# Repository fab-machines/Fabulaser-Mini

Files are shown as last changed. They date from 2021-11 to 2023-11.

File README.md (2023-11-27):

<div align="center"><h1 style=align="center">Fabulaser Mini V3</h1></div>
<div align="center"><i>An open source laser cutter within your reach.</i></div>

<br>
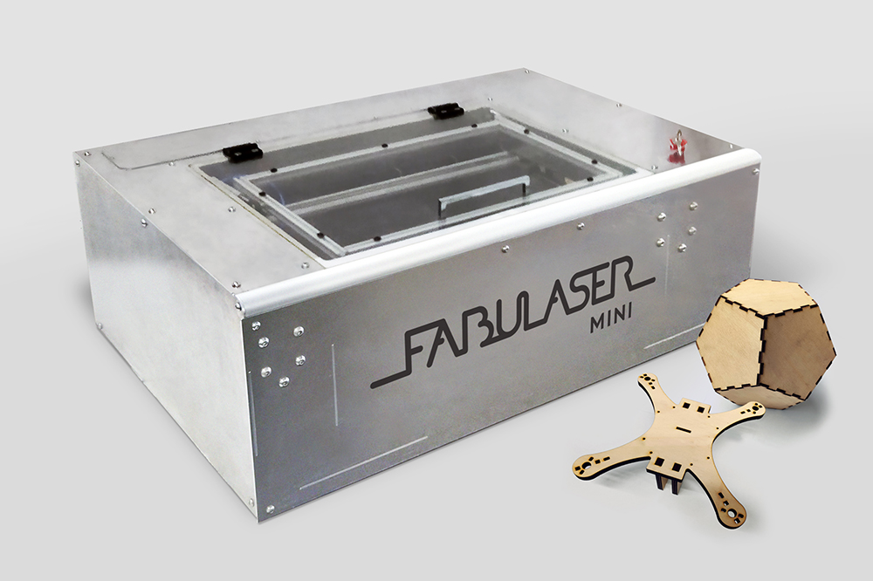
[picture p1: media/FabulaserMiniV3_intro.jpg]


Introduction 
---
Fabulaser Mini is a compact, yet  powerful, open source laser cutter. Developed to fit in Fab Labs and classrooms, Fabulaser Mini aims to lower the boundaries of accessing laser cutting technology, representing an ideal compromise between performance and cost. With an optimized 40W CO2 laser, it is able to cut 8mm acrylic, and with a cutting area of 600x400mm is one the largest of this machine category. The compact machine size of 1161x812x390mm, allows the usage in small rooms with a normal table or a desk.

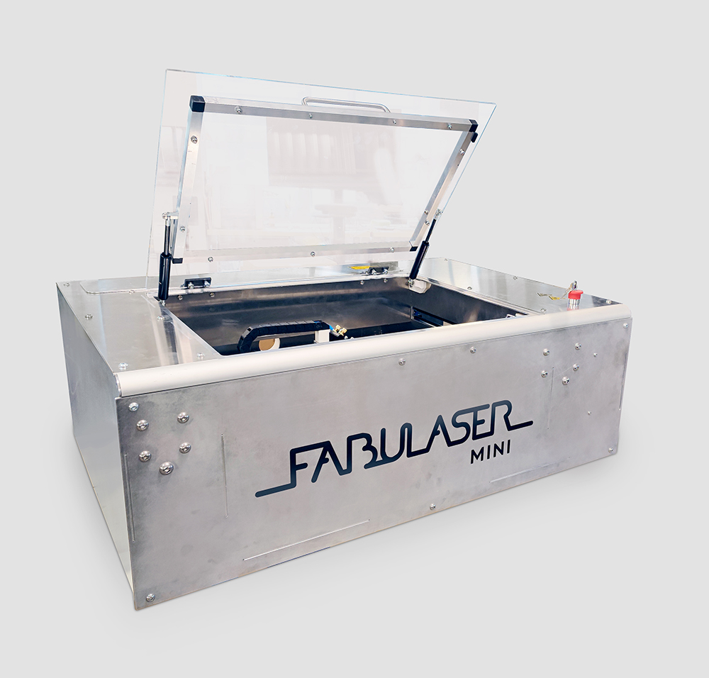
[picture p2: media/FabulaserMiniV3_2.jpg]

<br>

A tool to make, a tool to learn.
--

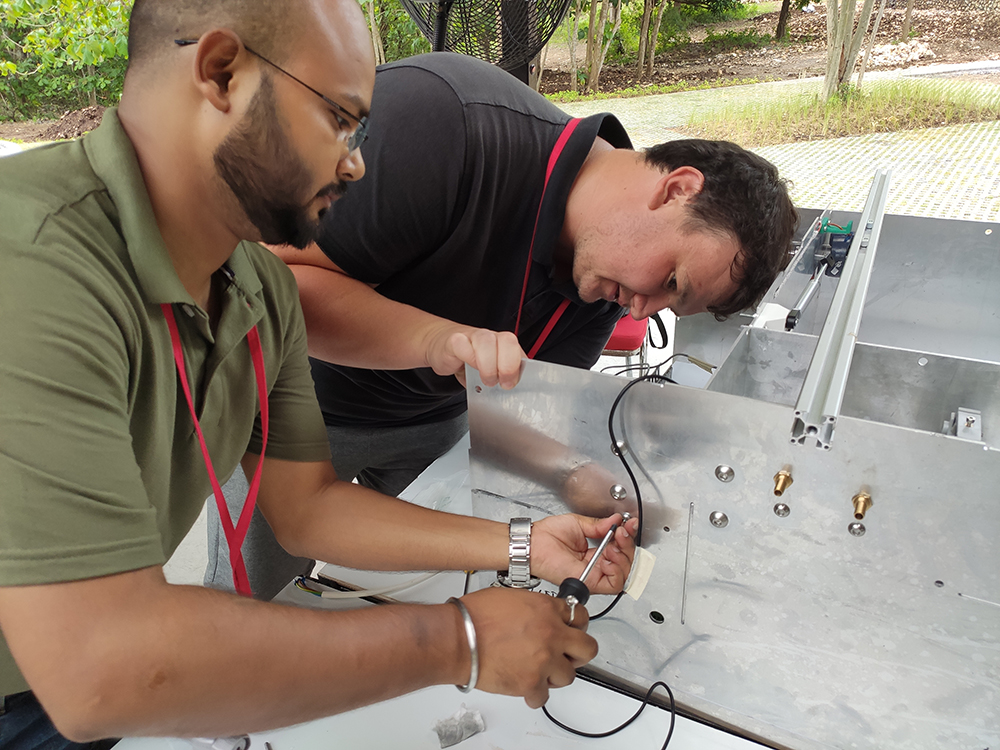
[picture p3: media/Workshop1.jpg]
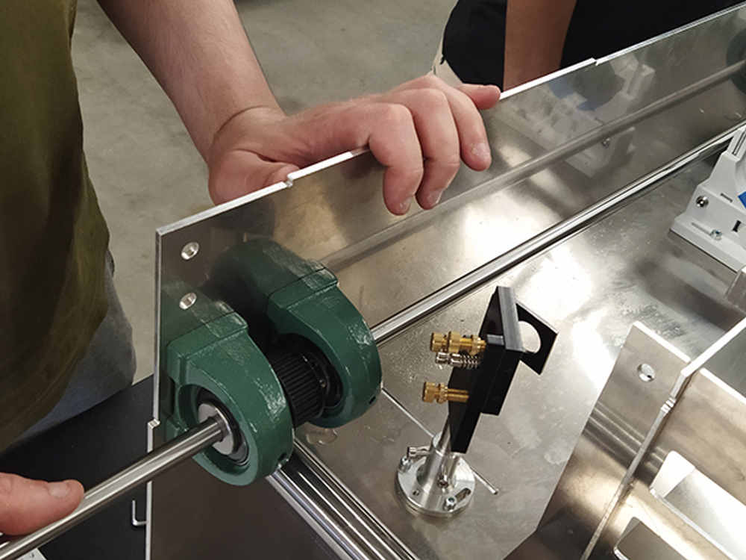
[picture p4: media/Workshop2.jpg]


In comparison to commercial laser cutters, Fabulaser Mini adds on top of the laser cutting functionalities a valuable learning experience. Ideally built together with students during a workshop, Fabulaser Mini will give to the user not only the possibility to laser cut, but also to learn how the machine is made, how it works. And other than learning about electronics, mechanics and lasers, the final user will also have a deep knowledge of the machine, so to be able to efficiently execute maintenance, apply improvements and even design his own machine later on!

The Assembly Manual 
--
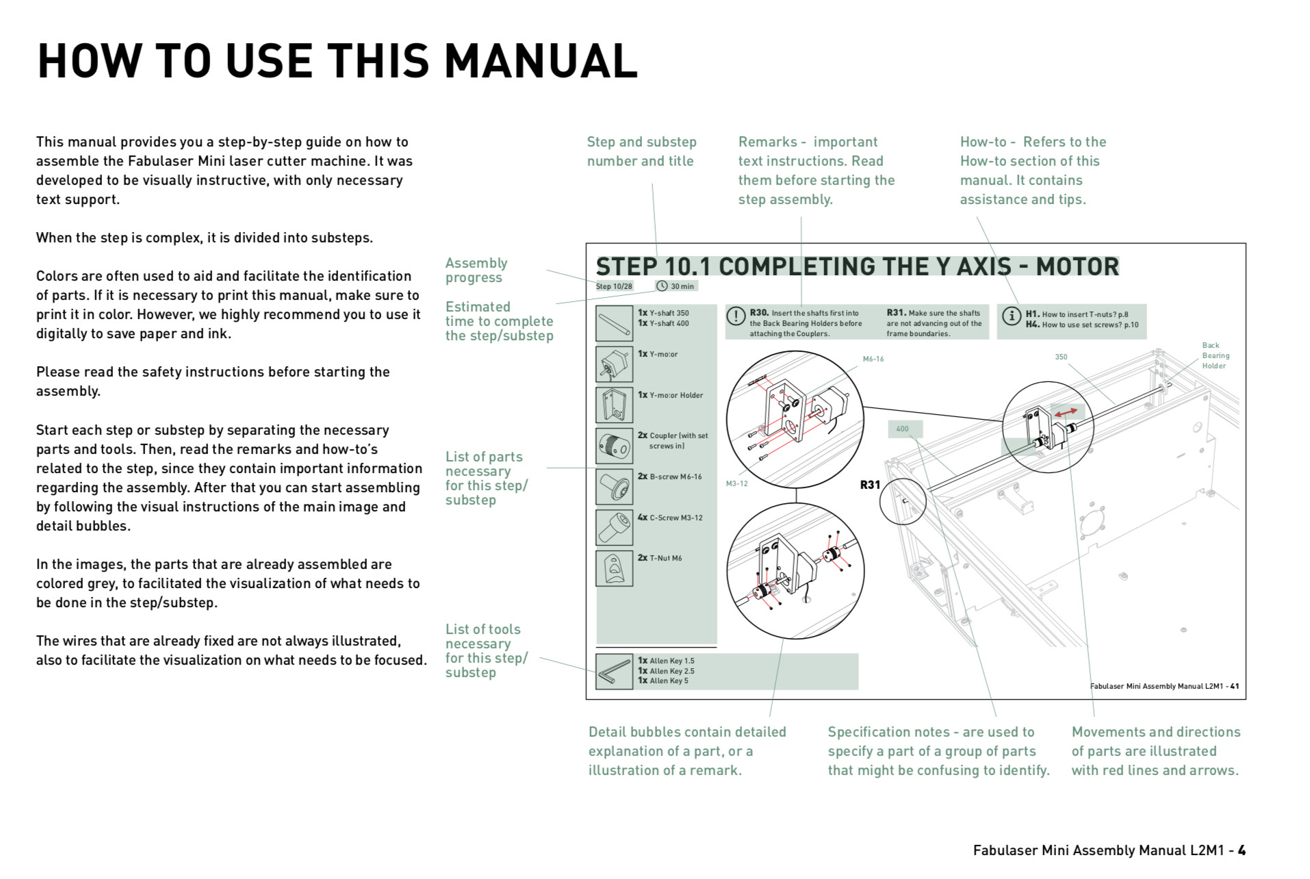
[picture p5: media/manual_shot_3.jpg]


Fabulaser Mini comes with a state of art building instruction manual, detailing any of the many building details. Divided in logical steps, the manual also instructs on general building practices, the laser calibration and how to connect all the electronics of the machine. Teachers and lectures can also use the manual to divide workshop participants into building groups.
<div><i>Fabulaser Mini V3 assembly manual is still in progress. The complete manual is available only for Fabulaser Mini V2</i></div>

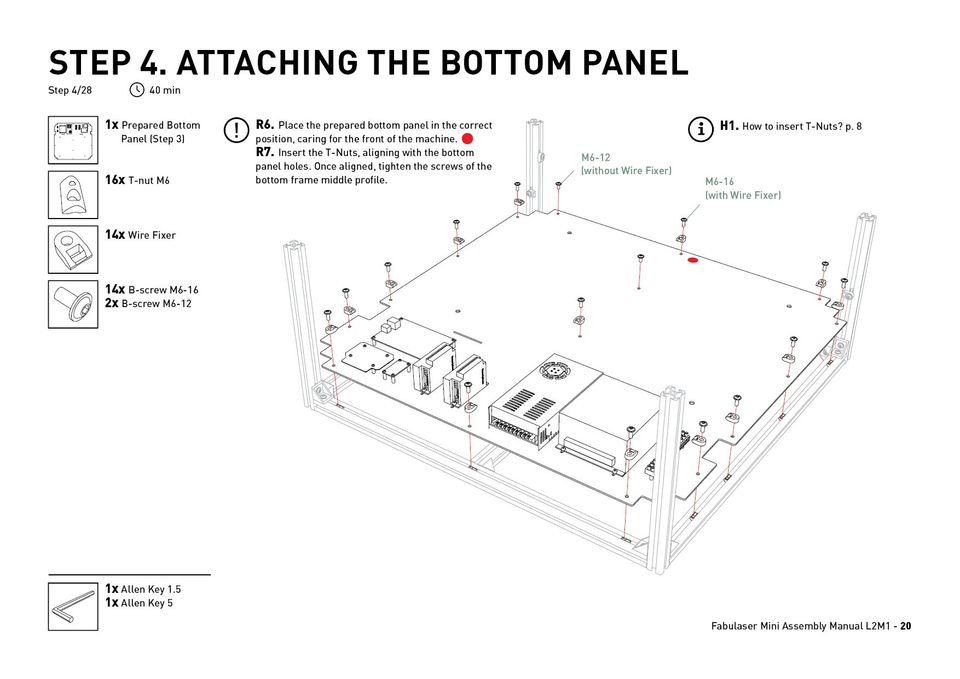
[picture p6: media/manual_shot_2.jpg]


The Kit
--

Fabulaser Mini kit, is the one-stop solution for everything you need to fully use the laser cutting capabilities of Fabulaser Mini. Providing all the required parts and special tools to build the laser cutter, Fabulaser Mini kit also provides all the additional accessories to start laser cutting out of the box. As well as all the required adapters and connections are provided, so that the user only have to concentrate on assembly, without losing time in searching and buying additional parts.

Included in the Fabulaser Kit:

- Fabulaser Mini machine parts
- air assist compressor
- exhaust radial fan
- indoor air filter
- water chiller
- all the required connections/adapters

More info on Fabulaser Mini are available at: [http://fabulaser.net/](http://fabulaser.net/)

Fabulaser Mini V3 specifications
--
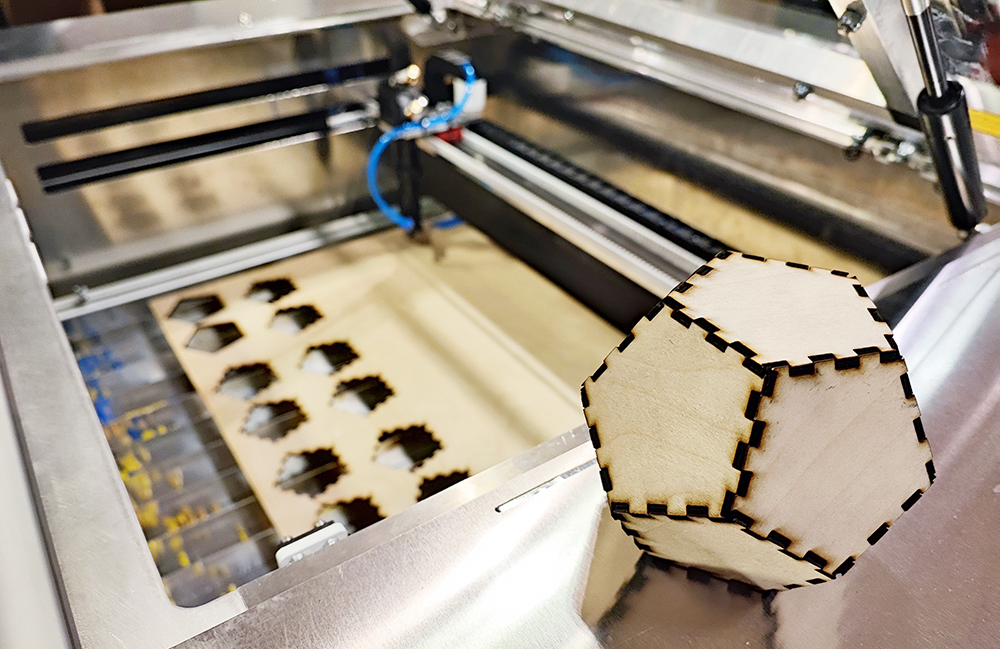
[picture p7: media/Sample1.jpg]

<br>

- laser source: 40W CO2
- cutting area: 600x400mm
- resolution: 0.05mm 
- max. cutting thickness: 
  - 10mm acrylic
  - 6mm MDF
  - 8mm Plywood
- max speed: 1000mm/s
- motion: linear rails and linear shafts
- frame and housing: interlocked aluminum plates
- bed: aluminum lamella
- sensors: inductive probes
- controller: 32bit Teensy 4.1
- firmware: [grbl-hal]([https://github.com/cprezzi/grbl-LPC](https://github.com/grblHAL/iMXRT1062))
- machine dimensions: 1161x812x390mm

Files
--

- **[BOM](Fabulaser_Mini_V3_BOM.pdf)**
- **[Firmware](firmware)**
- **[CAD](cad)**
- **[Settings](settings)**
- **[Workbook](Fabulaser_Mini_V3_Workbook.pdf)**
- **[Wiring Schematic](WiringSchematic_FabulaserMini_V3.pdf)**
- **[Assembly Manual (Fabulaser Mini V2)](Fabulaser_Mini_V2_manual_L2M2.pdf)**

Authors
--

Fabulaser Mini has been designed, developed and manufactured by:<br>

- **Daniele Ingrassia, daniele@inmachines.net**
- **[InMachines Ingrassia GmbH](https://www.inmachines.net/)**<br>

License
--

The Fabulaser Mini hardware design, CAD and PCB files, BOM, settings and relative files are are released under the following open source license:

- CERN Open Hardware Licence Version 2 Weakly Reciprocal - **[CERN-OHL-W](LICENSE_CERN_OHL_W_V2.txt)**

The Fabulaser assembly manual, pictures and presentation text of this repository are released under the following license:

- Creative-Commons-Attribution-ShareAlike 4.0 International - **[CC BY-SA 4.0](LICENSE_CC_BY_SA_4.0.txt)**

Fabulaser Mini uses grbl-LPC [https://github.com/cprezzi/grbl-LPC](https://github.com/cprezzi/grbl-LPC), released under the [GPLv3 license](https://www.gnu.org/licenses/gpl-3.0.en.html).

Previous version
--

Previous versions of Fabulaser Mini will always be available. 

**[Fabulaser Mini V2 Repository](Fabulaser_Mini_V2)** 
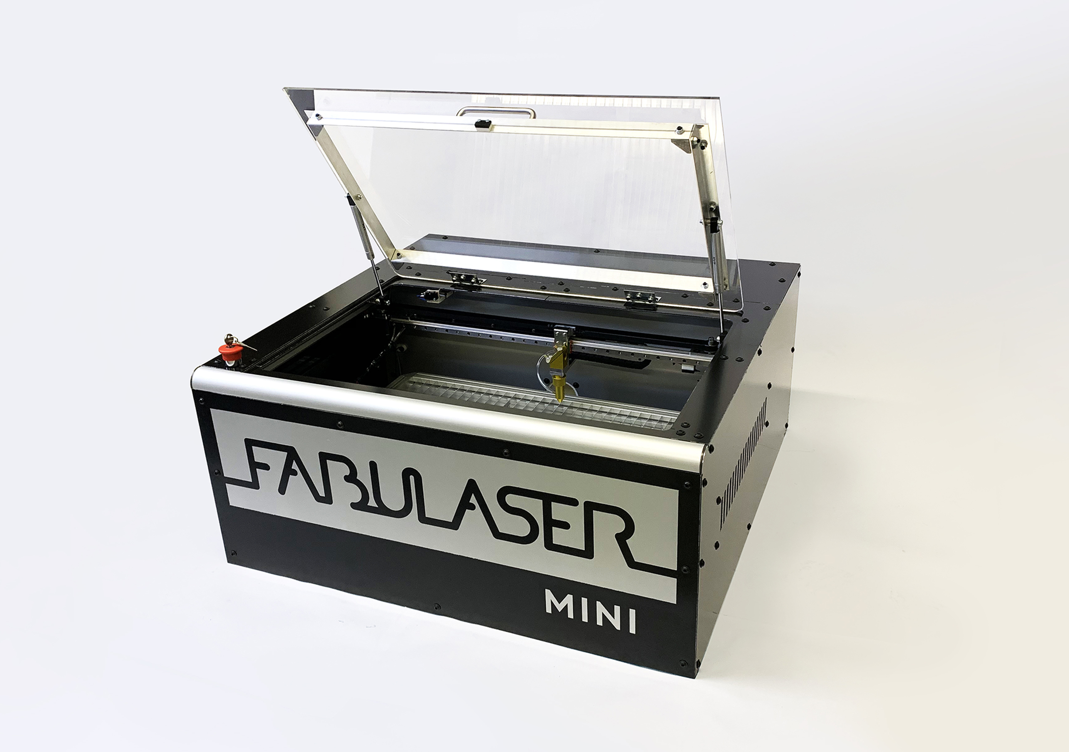
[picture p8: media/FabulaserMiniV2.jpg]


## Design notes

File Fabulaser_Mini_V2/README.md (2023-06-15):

<div align="center"><h1 style=align="center">Fabulaser Mini V2</h1></div>

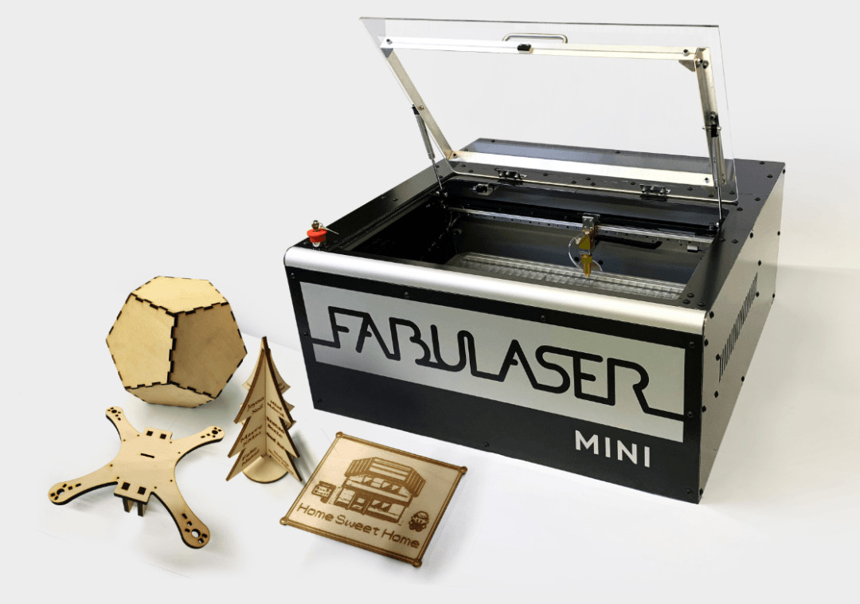
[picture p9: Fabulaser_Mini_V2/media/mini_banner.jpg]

<div align="center"><i>An open source laser cutter within your reach.</i></div>

Introduction 
---
Fabulaser is a compact, yet  powerful, open source laser cutter. Developed to fit in Fab Labs and classrooms, Fabulaser Mini aims to lower the boundaries of accessing laser cutting technology, representong an ideal compromise between performance and cost. With an optimized 40W CO2 laser, it is able to cut 8mm acrylic, and with a cutting area of 600x400mm is one the largest of this machine category. The compact machine size of 870x810x380mm and the weight under 60kg, allows the usage in small rooms with a normal table or a desk.

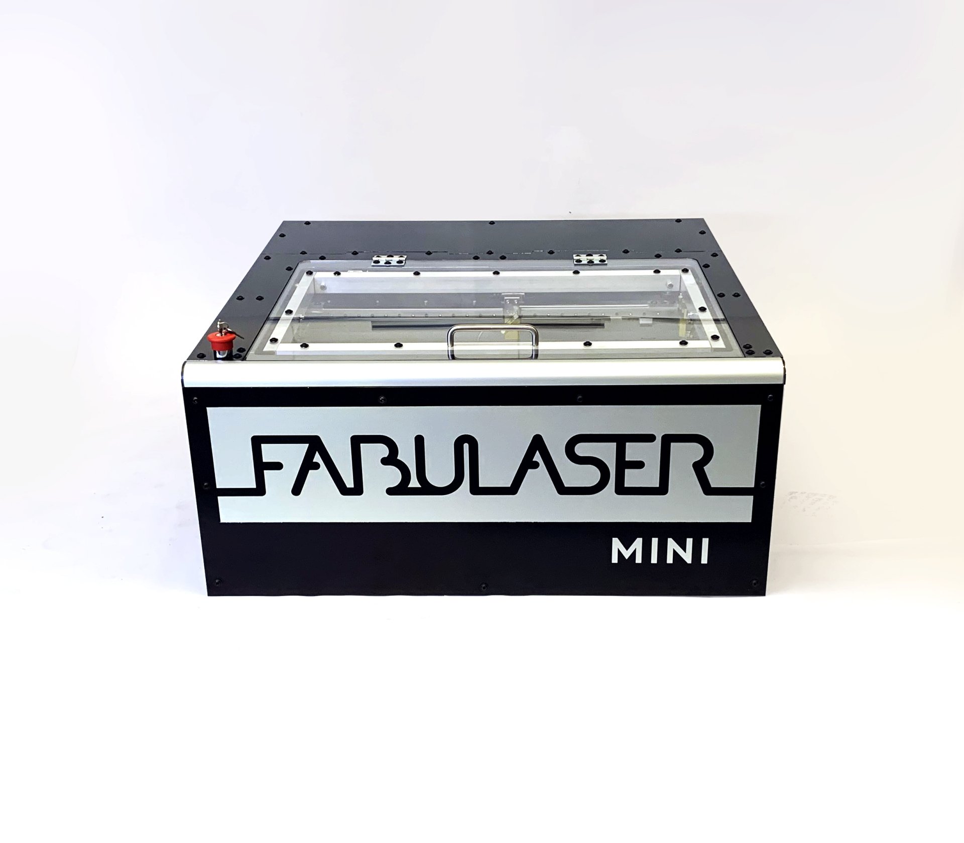
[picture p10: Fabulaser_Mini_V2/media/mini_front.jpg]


A tool to make, a tool to learn.
--
In comparison to commercial laser cutters, Fabulaser Mini adds on top of the laser cutting functionalities a valuable learning experience. Ideally built together with students during a workshop, Fabulaser Mini will give to the user not only the possibility to laser cut, but also to learn how the machine is made, how it works. And other than learning about electronics, mechanics and lasers, the final user will also have a deep knowledge of the machine, so to be able to efficiently execute maintenance, apply improvements and even design his own machine later on!

The Assembly Manual
--



Fabulaser Mini comes with state  of art building instruction manual, detailing any of the many building details. Divided in logical steps, the manual also instructs on general building practices, the laser calibration and how to connect all the electronics of the machine. Teachers and lectures can also use the manual to divide workshop participants into building groups.
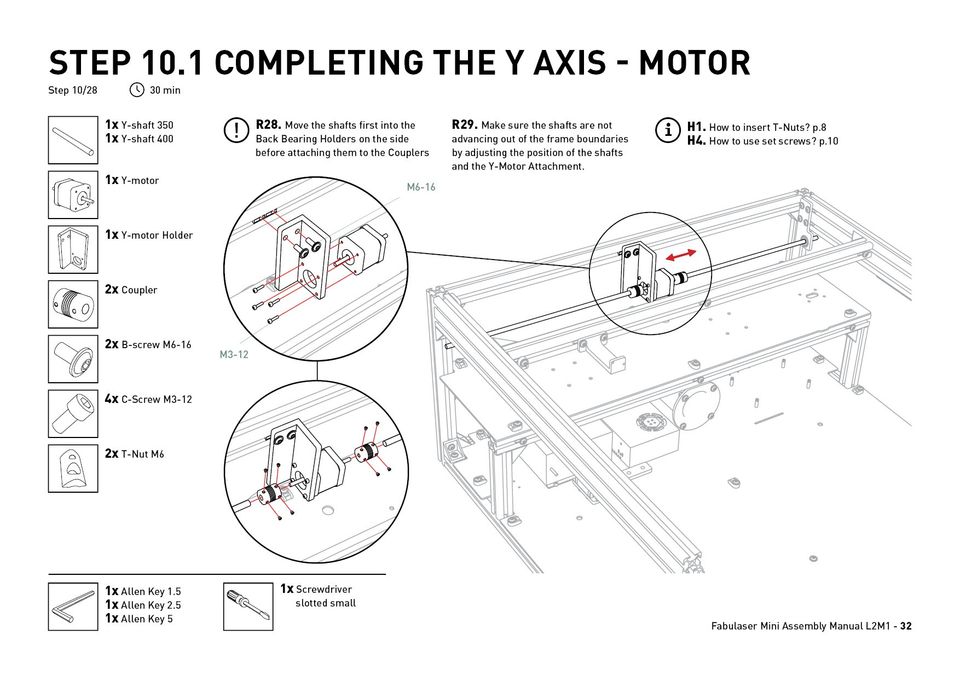
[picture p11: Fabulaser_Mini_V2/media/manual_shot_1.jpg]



The Kit
--
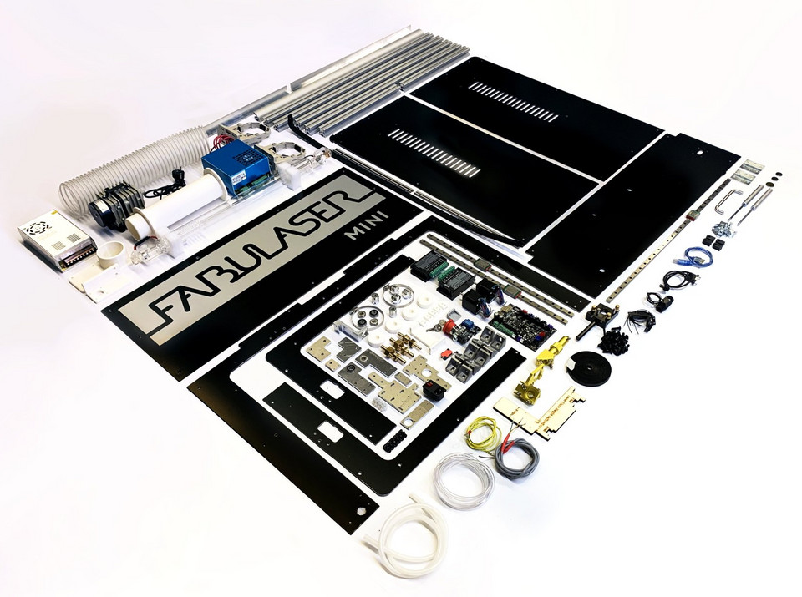
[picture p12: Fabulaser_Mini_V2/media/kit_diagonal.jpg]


Fabulaser Mini kit, is the one-stop solution for everything you need to fully use the laser cutting capabilities of Fabulaser Mini. Providing all the required parts and special tools to build the laser cutter, Fabulaser Mini kit also provides all the additional accessory to start laser cutting out of the box. As well all the required adapter and connection are provided, so that the user only have to concentrate on assembly, without losing time in searching and buying additional parts.

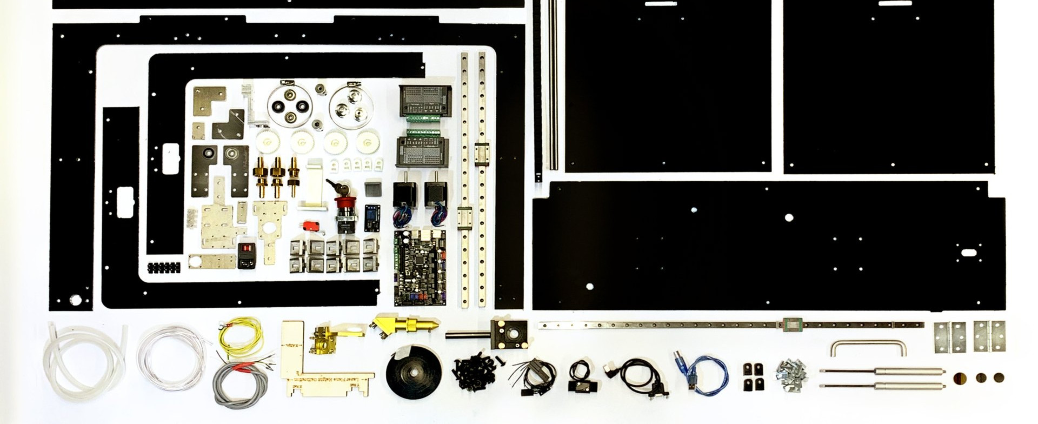
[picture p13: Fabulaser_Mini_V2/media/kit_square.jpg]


Included in the Fabulaser Kit:

- Fabulaser Mini machine parts
- air assist compressor
- exhaust radial fan
- indoor air filter
- water chiller
- all the required connections/adapters

More info on Fabulaser Mini are available at: [http://fabulaser.net/](http://fabulaser.net/)

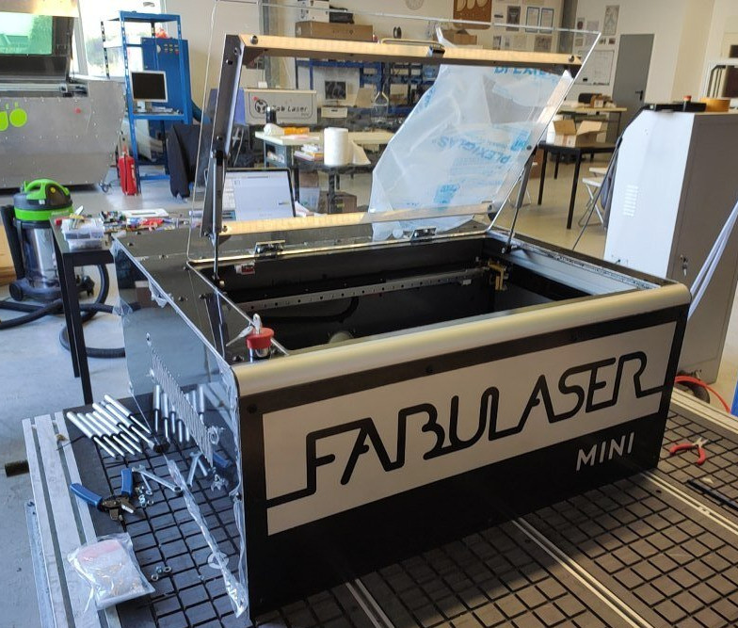
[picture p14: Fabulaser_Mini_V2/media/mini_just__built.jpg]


Fabulaser Mini specifications
--
- laser source: 40W CO2
- cutting area: 600x400mm
- resolution: 0.05mm 
- max. cutting thickness: 
  - 8mm acrylic
  - 6mm MDF
  - 8mm Plywood
- max speed: 400mm/s
- motion: linear rails
- housing: aluminum composite
- bed: aluminum lamella
- frame: aluminum profiles
- controller: 32bit LPC1768
- firmware: [grbl-LPC](https://github.com/cprezzi/grbl-LPC)
- machine dimensions: 870x810x380mm

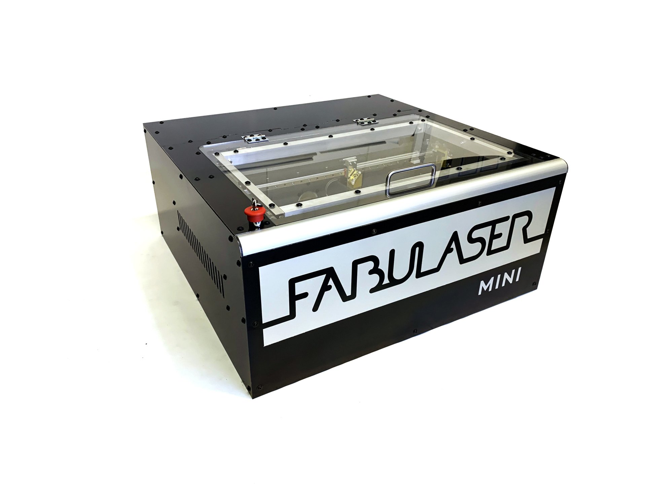
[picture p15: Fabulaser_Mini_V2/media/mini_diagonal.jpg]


Files
--
- **[Assembly manual](manual)**
- **[BOM](Fabulaser_V2.1_BOM.pdf)**
- **[Firmware](firmware)**
- **[CAD](cad)**
- **[Converter PCB](converterPCB)**
- **[Settings](settings)**
- **[User manual](Fabulaser_User_manual_L2M1.pdf)**

Authors
--

The Fabulaser Mini Assembly Manual authors are:<br>
- **Marc Kohlen, marckohlen@3dinx.com**
- **Liane Sayuri Honda, licasayurih@gmail.com** 

Fabulaser Mini has been designed, developed and manufactured by:<br>

- **Daniele Ingrassia, daniele@inmachines.net**
- **[InMachines Ingrassia GmbH](https://www.inmachines.net/)**<br>

License
--

The Fabulaser Mini hardware design, CAD and PCB files, BOM, settings and relative files are are released under the following open source license:

- CERN Open Hardware Licence Version 2 Weakly Reciprocal - **[CERN-OHL-W](LICENSE_CERN_OHL_W_V2.txt)**

The Fabulaser assembly manual, pictures and presentation text of this repository are released under the following license:

- Creative-Commons-Attribution-ShareAlike 4.0 International - **[CC BY-SA 4.0](LICENSE_CC_BY_SA_4.0.txt)**

Fabulaser Mini uses grbl-LPC [https://github.com/cprezzi/grbl-LPC](https://github.com/cprezzi/grbl-LPC), released under the [GPLv3 license](https://www.gnu.org/licenses/gpl-3.0.en.html).

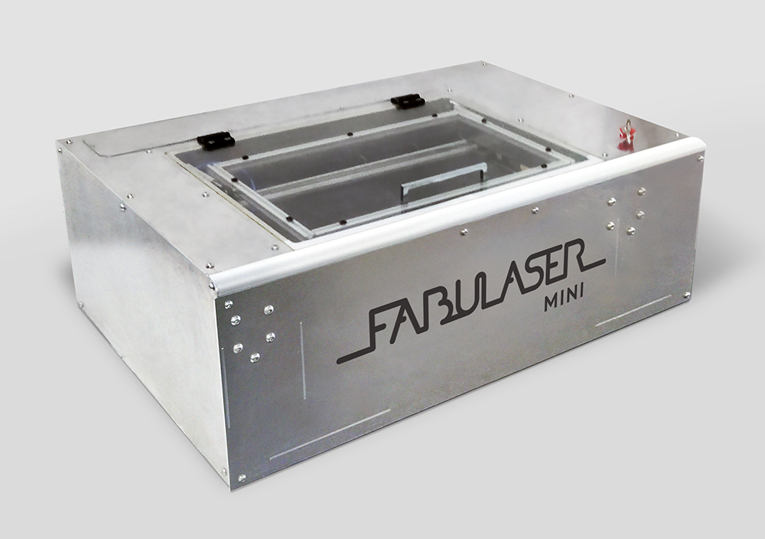
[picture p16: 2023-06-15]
media/FabulaserMiniV3.jpg

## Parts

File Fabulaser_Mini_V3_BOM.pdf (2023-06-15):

External Accessories
Power Cord (computer style) at least 2m | 1
Foot switch | 1
Air Filter Airmex AM03 or similar | 1
Water Chiller CW-3000 | 1
Air pump Hailea ACO-318 | 1
Radial Fan 150mm 150W Neverest RV-B | 1
Water Pipe Outside inside diameter 9mm | 2
Water Pipe Inside Silicon 1m 10x7mm | 2
Air pipe 6x4mm 5m | 1
Air pipe adapter 6-10mm with pipe 10mm | 1
Safety Sticker set | 1
USB Cable outside 2m or more | 1
Exhaust hose 80mm 3m | 2
Hose Clamps 80mm | 4
Tesa Double Side Tape 50mm 5m | 2
Fuse 6.3A 5x20mm | 2
Filter Adapter 3D Prined | 1
Radial Fan Adapter 3D Prined | 2
Focus Tool | 2
Rubber Rings 20mm | 2
Optical Paper | 1
Wago Connectors Set | 1
Cable Ties min. 150mm 100 pieces | 1

X Axis
Ball Bearing 6801 | 4
Stepper Motor 24HS39-4204D with Cable 4x0.5mm 150cm ground shield | 1
X Plate Aluminum 8mm | 1
X Belt HTD 5M 10 2075mm | 1
Y Linear Bearing SCE25UU Left | 1
Y Linear Bearing SCE25UU Rigth | 1
X Linear Guide HGR15 T 850mm | 1
X Left Pulley HTD 5M 28T 9mm | 1
X Right Pulley HTD 5M 28T 9mm | 1
X Shaft 12mm 35mm | 1

Y Axis
Y Shaft 25mm 800mm Tapped M12 | 2
Y Belt HTD 5M 15mm 2000mm cut to 1525mm | 2
Stepper Motor 24HS39-4204D with Cable 4x0.5mm 100cm ground shield | 1
Shaft 12mm 150mm | 1
Shaft 12mm 100mm | 1
Shaft 12mm 1000mm | 1
Y Motor Holder 3D Printed With Inserts M8 | 1
Y Belt Attacher Aluminum 6mm | 4
Y Pulley HTD 5M 26T 9mm | 1
Y Pulley HTD 5M 16T 9mm | 1
Y Pulley HTD 5M 26T 15mm (3) | 4
Y Motor Belt HTD 5M 9mm 305T | 1

Pillow Block 12mm UCPA201 (3) | 8

Housing
Front Panel Aluminum 4mm | 1
Right Panel Aluminum 3mm | 1
Separator Panel Aluminum 3mm | 1
Laser Panel Aluminum 3mm | 1
Cover Panel Aluminum 3mm | 1
Window Spacer Left Aluminum 3mm | 1
Window Spacer Back Aluminum 3mm | 1
Window Spacer Right Aluminum 3mm | 1
Sub Window Front Aluminum 3mm | 1
Sub Window Right Aluminum 3mm | 1
Sub Window Left Aluminum 3mm | 1
Sub Window Back Aluminum 3mm | 1
Inner Panel Left Aluminum 3mm | 1
Inner Panel Right Aluminum 3mm | 1
Back Panel Aluminum 4mm | 1
Left Panel Aluminum 3mm | 1
Top Panel Aluminum 3mm | 1
Bottom Panel Aluminum 3mm | 1
Front Support 3D Printed | 1
Top Aluminum Profile 30x60 Nut 8 800mm | 2
Bottom Aluminum Profile 30x30 Nut 8 800mm | 3
Fillet Aluminum Profile 30x30 Nut 8 1145mm | 1
Front Bracket 30x20x3 200mm | 1
Exhaust Adapter 3D Printed | 1
Water Connector 9-9mm Screw 11.7mm | 2
Air Connector Press Fit 6-6mm | 1

Bed
Aluminum Profile 40x40 Nut 8 500mm | 2
Bed Bracket 40x40x3 700mm | 2
Bed Lamella Aluminum 35x40x0.8 | 16

Window
Window Front Profile Aluminum 20x20 599mm | 1
Window Left Profile Aluminum 20x20 380mm | 1
Window Right Profile Aluminum 20x20 380mm (1) | 1
Window Back Profile Aluminum 20x20 599mm | 1
Laser Window Acrylic 750x600 6mm | 1
Hinge GN 237-ZD-60-60-A-SW | 2
Window Connector 20x20 3D Printed | 2
Piston Support Right 3D Printed | 1
Piston Support Left 3D Printed | 1
Piston 100N Length 250 Travel 80mm | 2
Window Handler 192mm | 1
Window Angle Press Fit 20x20 | 4
Electrics / Electronics
USB Cable Inside | 1
Resistor 1K | 3

Cable Duct 25x40 700mm | 2
Stepper Motor Driver DM556T | 2
Motor Power Supply RSP-500-48A | 1
Inductive Probe LJ12A3-4-Z/AY with cable 3x0.25mm 320cm + 140cm ground shield | 2
Window Sensor PS-3150 with cable 2x0.25 160cm ground shield | 1
Window Magnet PS-3150 | 1
Logic Power Supply LRS-100-24 | 1
Laser Power Supply MYJG50W | 1
Window Sensor Holder 3D Printed | 1
Cable Chain inner size 25x18 outer size 35x23 1000mm | 1
Power Plug 48x28x27mm M4 | 1
Cable Chain inner size 15x15 outer size 24x20 2000mm | 1
X Chain Spacer 3D Printed | 1
Y Endstop Holder 3D Printed | 1
X Endstop Holder Pom 6mm | 1
Y Cable Organizer 3D Printed | 1
Chiller Connector 3 Pole with 20cm 2x0.25mm cable no shield (3 cores used) | 1
Emergency Button With Key AS22-B142 | 1
M12x1.5 Cable gland v1 | 2
Controller PCB | 1
Pipe Holder M6 10mm | 2
Wire Fixer | 6
Driver Power Cable 2x1mm 60cm ground shield | 2
Controller Power Cable 2x1mm 70cm ground shield | 1
Driver Logic Cable 4x0.5mm 40cm ground shield | 2
Laser Logic Cable 3x0.25 90cm ground shield | 1
Chiller Cable 2 cores min. outer diameter 6.5mm 2m with 2 x chiller connectors | 1
Mains Cable AC 3x1.5mm 25cm | 1
AC Jumper 1x1.5mm 8cm | 1
Earth Cable AC 1x1.5mm 15cm | 1
AC Power Cable 3x1.5mm 20cm | 3
AC Extension Cable 3x1.5mm 25cm | 1
Emergency Button Cable 2x1.5mm 110cm | 1
Led Strip 24V Warm White 40cm with cable 2x0.75 70cm + 2x0.75 230cm | 2

Laser
Laser connector (screw terminal mammut) 2 pos | 2
Laser Mirror 25mm | 3
Laser Lens 20mm 50.8mm | 1
First Mirror Holder 25mm | 1
Laser Tube Holder 45-80mm | 2
Laser Tube CO2 40W 50x720mm | 1
Second Mirror Holder 25mm | 1
Laser Mirror Spacer 3D Printed | 1
Laser Head Mirror 25 Lens 20 | 1

Head
Head Holder Aluminum 6mm | 1
X Carriage QHH15CA1T1200Z0C | 1
Belt Attacher Aluminum 6mm | 1

Fasteners
ISO 7380 M10 12mm | 16
ISO 7380 M8 10mm | 38
ISO 7380 M5 25mm | 4
ISO 7380 M4 10mm | 37
ISO 7380 M12 20mm | 4
ISO 7380 M8 20mm | 24
DIN 912 M5 12mm | 22
DIN 912 M6 16mm | 8
DIN 912 M5 16mm | 8
DIN 912 M4 16mm | 4
DIN 912 M3 8mm | 6
DIN985 M8 | 34
DIN 985 M5 | 8
Plastic DIN 7985 M3 8mm | 6
Nut 8 M8 | 16
Nut 6 M5 | 3
Nut 6 M4 | 2
DIN 125 M8 | 2
ISO 7380 M8 55mm | 2
DIN 985 M6 | 12
ISO 7380 M6 35mm | 9
DIN 912 M3 12mm | 4
DIN 985 M3 | 4
DIN 7991 M8 25mm | 4
DIN 9021 M8 Washer | 4
DIN 912 M4 35mm | 5
ISO 7380 M8 30mm | 6
Standoff M8 15-8 Male-Female | 2
DIN 912 M4 12mm | 9
DIN 912 M4 10mm | 8
DIN 912 M8 130mm | 4
DIN 912 M3 6mm | 5
DIN 7991 M8 50mm | 4
DIN 912 M5 30mm | 4
ISO 7380 M6 16mm | 2
ISO 7380 M8 16mm | 2
Standoff Male Female M3 20mm | 4
DIN 933 M6 16mm | 1
DIN 933 M6 20mm | 1

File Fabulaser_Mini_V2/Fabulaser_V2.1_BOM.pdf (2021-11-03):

Ready Made Parts External Manual name | Specifications | Amount | Price | Total | Shipping | Vendor | Label Name | Checks / ToDo | Notes
Air Filter | Airmex AM 03 / 6001 Cw-3000 | 1 1 | €499.00 €100.00 | €499.00 €100.00 | €0.00 €0.00 | link (https://www.airmex.de/Loetrauchabsaugung_AirMex-6001M) link | Water Chiller Air Filter | Power Plug; Attach filter adapter w/ silicon Water Chiller Power Plug; Accessories | about price
Air Compressor | 10x80mm ACO-318 | 1 3 | €31.80 €0.89 | €31.80 €2.67 | €0.00 €0.00 | link (https://www.ebay.de/itm/Hailea-Sauerstoffpumpe-Teichbel%C3%BCfter-ACO-208-318-328-388-009/272308840043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) link | Air Compressor Hose Clamps | Power Plug; Brass Adapter Hose Clamps
Exhaust Hose | Diameter 80mm Lenght 1500mm meters | 2 | €2.75 | €5.50 | €7.00 | link (https://www.ebay.de/itm/10m-Kunststoffschlauch-mit-Drahtspirale-Luftungsschlauch/223031773874) | Exhaust Hose | Remove Final Part Metal Wire
Teflon Tape | Teflon Tape 12mm | 1 | €0.80 | €0.80 | €0.00 | link (https://www.ebay.de/itm/0-05-m-10-Rollen-PTFE-Band-weis-12-m-x-12-mm-Teflonband-Gewindeband-Dichtband/173879877404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) | Teflon Tape Radial Fan | 150mm 533m3/h | 1 | €60.00 | €60.00 | €0.00 | link | Radial Fan | Attach 2xRadial Fan Connector (if without Power Plug: attach it) | better find one with smaller diameter and more power Double-sided Tape | Double side tape, TESA Extra Strong for Bed Lamella, in meters | 3 | €0.60 | €1.80 | €0.00 | link | Double-sided Tape | easy to find at hardware market Cable Ties | Cable Ties Package 2.5x140mm 100 pieces | 1 | €4.00 | €4.00 | €0.00 | link | Cable Ties Red Dot Stickers | 4 | Red Dot Stickers
Electrics / Electronics Manual name | Specifications | Amount | Price | Total | Shipping | Vendor1 | Label Name | Notes
Emergency Button | Emergency button with key AS22-B142 3m shielded, 90 connector Panel mount USB B | 1 1 1 | €5.99 €2.59 €2.19 | €5.99 €2.59 €2.19 | €4.90 €2.49 €0.00 | link (https://www.ebay.de/itm/Notausschalter-Not-aus-Schalter-Druck-Notschalter-Auschalter-Druckschalter/281817794707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) link link | Emergency Button USB Cable Inside USB Cable Inside USB Cable | Attach 2 Plastic Screws M3-8 USB Cable
Laser Power Supply | 40W CO2 Power Supply | 1 | €35.00 | €35.00 | €0.00 | link (https://www.ebay.de/sch/i.html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) | Laser Power Supply | Remove Right Most Connector; Attach Crimp @ end of red cable | about price, also at 35€
Laser Controller | MKS Sbase | 1 | €35.00 | €35.00 | €0.00 | link (https://www.aliexpress.com/item/32384368763.html?spm=a2g0s.9042311.0.0.2fd64c4d9dnc0p) | Laser Controller | Upload Firmware; remove jumper | about price, best from China Motor Driver | TB6600 | 2 | €7.00 | €14.00 | €0.00 | link | Motor Driver | Check all connectors are present | about price, best from China Relay | single channel | 1 | €2.00 | €2.00 | €1.65 | link | Relay | Test it | about price, best from China Motor Power Supply | 24V 15A | 1 | €20.00 | €20.00 | €0.00 | link | Motor Power Supply | Check internal label for correctness | about price, best from China Window Switch | V-156-1C25 | 1 | €2.79 | €2.79 | €1.99 | link | Window Switch | Test it with the cable

about price, best from China

Window Sensor | PS-3150
3 | €3.00 | €8.99 | €0.00 | link (https://www.ebay.de/itm/PS-3150-Turschalter-Magnetschalter-Fenster-Reed-Switch-Turkontakt-P-3150-m-Kabel/123267796554)
Window Sensor | Test it with the cable Window Magnet | PS-3150 | Window Magnet
Y-endstop Sensor | PS-3150 | Y-endstop Sensor + X-endstop Sensor + Endstop Cable | Test it with cable X-endstop Sensor | PS-3150
X-endstop Magnet | PS-3150 | X-endstop Magnet
Y-endstop Magnet | PS-3150 | Y-endstop Magnet Cable Wrapper | 1m 4mm+ | 1 | €0.60 | €0.60 | €0.00 | link | Cable Wrapper | about price, best from China
Foot Switch | 240V Eco Line Comfort Switch Adapter | 1 | €11.13 | €11.13 | €2.99 | link (https://www.ebay.de/itm/BRENNENSTUHL-Eco-Line-Comfort-Switch-Adapter/233743985229?epid=22011384030) | Foot Switch
Terminal Block | 4 Positions, minimum 1.5-2.5mm2 | 2 | €0.89 | €1.78 | €0.00 | link (https://www.ebay.de/itm/Lusterklemmen-12-polig-Listerklemmen-Verbindungsklemmen-1-5-16mm-Lampen-Klemme/153006846657) | Terminal Block | Check that the terminal block fits to the bottom panel; add extra
Laser Attachments | Terminal Block + heat shrinking tubes | 10 | €0.10 | €1.00 | €0.00 | | Laser Attachments | fits to the laser tube | about price
Power Cable | PC Power Cable | 1 | €4.50 | €4.50 | €0.00 | link (https://www.ebay.de/itm/Manhattan-Powerkabel-Stromkabel-PC-Drucker-Monitor-Fernseher-1-5m-Schwarz/253379816568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) | Power Cable
Power Plug | Main Power Plug Inlet+Power switch, 1.5 or 2mm panel spacing Cable Chain 8x8-R18 1000mm | 1 1 | €2.50 €8.99 | €2.50 €8.99 | €2.99 €4.90 | link (https://www.ebay.de/itm/Kaltgeratestecker-Stecker-mit-Rot-Schalter-IEC320-C14-10A-Sicherung-Einbaubuchse/223935140540) link | Power Plug + Mains Cable + Earth Cable Chain | check connections Chain
Fuse | 1K resistor 1/4W trough hole 6.3A 5x20mm | 2 1 | €0.29 €0.02 | €0.57 €0.02 | €0.00 €0.00 | link (https://www.ebay.de/itm/10x-Glassicherung-F-6-3-A-Flink-5x20mm-FSP-Sicherung-6300-mA-Feinsicherung-time/264578536585) link | Fuse | Attach laser logic cable->check connections Add extra Resistor
LED Strip | 2 x 30cm 5730, meters | 1 | €3.00 | €3.00 | €0.00 | link (https://www.amazon.de/gp/product/B088KP7DRG/ref=ppx_yo_dt_b_asin_title_o00_s00?ie=UTF8&psc=1) | LED Strip | Test it with the cable | about price, best from china
| Water Connector Inside 3/8 9mm Screw Inlet Specifications | Amount 2 | €1.75 Price | €3.50 Total | Shipping | Vendor1 | Water / Air Manual name Label Name | | Notes Water Connector Inside
| Water Connector Outside 3/8 9mm Screw | 2 | €1.00 | €2.00 | €5.00 €0.00 | link (https://www.ebay.de/itm/Gewindet%C3%BClle-mit-zylindrischen-Innengewinde-in-verschiedenen-Gr%C3%B6%C3%9Fe-Schlaucht%C3%BClle/301402581950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) link | Water Connector Outside Water Connector Inside | check visually Water Connector Outside check visually
Air Connector Inside | Air Connector Inside 3/8 6mm Screw Inlet | 1 | €1.75 | €1.75 | | link (https://www.ebay.de/itm/Gewindet%C3%BClle-mit-zylindrischen-Innengewinde-in-verschiedenen-Gr%C3%B6%C3%9Fe-Schlaucht%C3%BClle/301402581950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) | Air Connector Inside | check visually
Air Connector Outside | Air Connector Outside 3/8 9mm Screw Water Flow Sensor K40 replacement 1/2 9mm | 1 2 1 | €1.00 €2.90 €8.00 | €1.00 €5.80 €8.00 | | link (https://www.ebay.de/itm/Messing-Schlaucht%C3%BClle-Au%C3%9Fengewinde-in-verschiedenen-Abmessungen-Schlauchnippel/291300977153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) link link | Water Flow Connector Air Connector Outside Water Flow Sensor | Test it with the cable check visually Water Flow Connector check visually Water Flow Sensor | about price, best from China
Air Tube Outside | 10x7mm 200cm Silicone | 4 4 | €0.52 €2.50 | €2.08 €10.00 | €3.90 €2.10 | link link (https://www.ebay.de/itm/Silikonschlauch-Siliconschlauch-D1-25mm-lebensmittelecht-200-auch-Druckschlauch/263190368164) | | Clean inside if dirty Water Outlet Tube Inside Clean inside if dirty Water Inlet Tube Inside Clean inside if dirty Water Tube Outside
| 9x1.5mm 200cm PVC not bendable easily, meters 10x7mm 100cm Silicone, roughly divided in 2 10x7mm 50cm Silicone | | | | | | Water Outlet Tube Inside Water Inlet Tube Inside Water Tube Outside Air Tube Outside | Clean inside if dirty
Air Tube Inside | 5x7mm PVC 4 meters | 1 | €1.00 | €1.00 | €4.00 | link (https://www.ebay.de/itm/PVC-Schlauch-Gewebeschlauch-Druckluftschlauch-Wasserschlauch-klar-transparent/264504310263) | Air Tube Inside | Clean inside if dirty
Mechanics Manual name | Specifications | Amount | Price | Total | Shipping | Vendor1 | Label Name | Notes
Linear Guide Y | Linear Rail Y MGN12 500mm + MGN12H | 2 | €30.00 | €60.00 | €0.00 | link (https://www.ebay.de/sch/i.html?_from=R40&_trksid=p2047675.m570.l1313&_nkw=mgn12+500mm&_sacat=0) | Linear Guide Y | check block carriage | about price
Linear Guide X | Linear Rail X MGN12 700mm + MGN12H/MGN12C | 1 | €45.00 | €45.00 | €0.00 | link (https://www.amazon.de/-/en/s?k=mgn12+700mm&rh=p_76%3A419122031&dc&rnid=419121031) | Linear Guide X | check block carriage | about price
X-belt | GT2 10mm 2m | 1 | €13.00 | €13.00 | €0.00 | link (https://www.ebay.de/itm/GT2-2GT-Zahnriemen-10mm-Neopren-mit-Fiberglas-Kern-3D-Drucker-CNC-Linear/283834203707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) | X-belt
Y-belt | GT2 10mm 2m 40N | 2 1 | €13.00 €1.59 | €26.00 €1.59 | Y-belt Window Piston Left
| 50N | 1 | €1.59 | €1.59 | €5.00 | link (https://www.ebay.de/itm/30N-200N-Gasdruckfeder-Gasfeder-D%C3%A4mpfer-Klappenbeschlag-Kompressionsfeder-SILBER/171263340318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) | Window Piston Right Window Piston Left | Attach 2xPiston Attacher Window Piston Right Attach 2xPiston Attacher
Profile 3060-770 | Aluminum Profile 3060 Nut 8 770mm | 2 | €10.00 | €20.00 | €10.00 | link (https://www.ebay.de/itm/Alu-Profil-30-x-60-Nut-8-Bosch-Raster-Aluminiumprofil-Nutprofil-eloxiert/152247531820) | Profile 3060-770 | cut smoothly on the side
Profile 20-660 | Aluminum Profile 2020 Nut 6 660mm | 4 | €3.36 | €13.44 | | link (https://www.ebay.de/itm/ALU-Profil-Aluprofil-20x20-Nut-6-Bosch-Raster-Aluminium-aluprofil-eloxiert/150650616574) | Profile 20-660
Profile 20-700 | Aluminum Profile 2020 Nut 6 700mm | 1 | €3.36 | €3.36 | | | Profile 20-700
Profile 20-350 | Aluminum Profile 2020 Nut 6 350mm | 2 | €1.92 | €3.84 | | | Profile 20-350
Profile Fillet | Aluminum Profile Fillet 3030 Nut 8 860mm | 1 | €9.90 | €9.90 | | link (https://www.ebay.de/itm/Alu-Profil-30-x-30-Nut-8-LR-Halbrund-Bosch-Raster-Nutprofil-Alu-eloxiert/162734635747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) | Profile Fillet
Profile 30-800 | Aluminum Profile 3030 Nut 8 800mm | 5 | €5.44 | €27.20 | | link (https://www.ebay.de/itm/Aluprofil-30x30-Nut-8-Bosch-Raster-Aluminiumprofil-eloxiert-Top-aluprofil/162208744513) | Profile 30-800
Profile 30-860 | Aluminum Profile 3030 Nut 8 860mm | 1 | €6.12 | €6.12 | | | Profile 30-860
Profile 30-770 | Aluminum Profile 3030 Nut 8 770mm | 3 | €5.44 | €16.32 | | | Profile 30-770
Profile 30-600 | Aluminum Profile 3030 Nut 6 600mm | 2 | €4.08 | €8.16 | | | Profile 30-600 | Do M6 Tappings
Profile 30-400 | Aluminum Profile 3030 Nut 6 400mm | 2 | €2.72 | €5.44 | | | Profile 30-400 | Do M6 Tappings
Profile 30-350 | Aluminum Profile 3030 Nut 8 350mm | 2 | €2.72 | €5.44 | | | Profile 30-350
Profile 30-380 | Aluminum Profile 3030 Nut 8 380mm | 2 | €2.72 | €5.44 | | | Profile 30-380
Profile 30-150 | Aluminum Profile 3030 Nut 8 150mm | 2 | €1.36 | €2.72 | | | Profile 30-150
Bracket 30 | 30x30 Nut 6/8 | 30 | | | | | Bracket 30 | Add 2 extra
Bracket 20 | 20x20 Nut 5/6 | 4 | €1.00 | €8.00 | | link (https://www.ebay.de/itm/Winkel-20-Nut-6-Bosch-Raster-Alu-blank-ohne-Befestigung-Verbindungstechnik/161771850315) | Bracket 20
Bed Connector 20 | 20x20 Nut 5/6 removed alignments | 4 | | | | | Bed Connector 20 | remove sides to fit
Y-motor | Nema 17 48mm dual shaft ATC 17HS5425B | 1 | €10.70 | €10.70 | €6.00 €0.00 | link (https://www.omc-stepperonline.com/dual-shaft-nema-17-bipolar-1-8deg-44ncm-62-3oz-in-1-68a-2-8v-42x48mm-4-wires.html) | Y-motor | Crimp ends; Label the ends of the wires
X-motor | Coupler 8mm - 5mm Nema 17 48mm | 1 2 | €9.29 €1.99 | €9.29 €3.98 | | link (https://www.omc-stepperonline.com/sale.html/3pcs-of-nema-17-bipolar-59ncm-84oz-in-2a-42x48mm-4-wires-w-1m-cable-and-connector.html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) link | X-motor Coupler | Check that the holes fit Attach label ends Coupler
Y-shaft 350 | Y 8mm Shaft 350mm | 1 | €4.90 | €4.90 | €6.00 | link (https://www.ebay.de/itm/Prazisionswelle-Linearwelle-CF53-8mm-3D-Drucker-CNC-100mm-1150mm-Linearfuhrung/152605342502) | Y-shaft 350
Y-shaft 400 | Y 8mm Shaft 400mm | 1 | €5.60 | €5.60 | | | Y-shaft 400
Y-pulley Back | Y Pulley GT2 10mm 36T Hole 8mm | 2 | €4.29 | €8.58 | €3.00 | link (https://www.ebay.de/itm/GT2-Zahnrad-2GT-30-32-36-40-42-48-60-Riemenscheibe-Zahnriemenrad-CNC-3D-Druck/162855300333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) | Y-pulley Back | check shafts fit | 2 pulleys have to be bored to 10mm
Y-pulley Front | Y Pulley GT2 10mm 36T Hole 10mm | 2 | €4.29 | €8.58 | | | Y-pulley Front | Insert Y-Bearing Front; cut side | in general pulleys can be 5mm and then bored
X-pulley | X Pulley GT2 10mm 36T Hole 5 | 1 | €4.29 | €4.29 | | | X-pulley | check that fits the motor
Y-bearing Back | Y Back Bearing 628 | 2 | €0.88 | €1.76 | €0.00 | link (https://www.ebay.de/itm/251241386645)
Y-bearing Front | Y Back Bearing MR106 | 10 | €0.66 | €6.60 | €0.00 | link (https://www.ebay.de/itm/20-Stk-Kugellager-6-10-3mm-Da-10mm-Di-6mm-Breite-3mm-MR106ZZ-Radiallager/231568015282)
X-bearing | Window Handler Hole distance 128mm 636Z | 1 1 | €1.00 €2.10 | €1.00 €2.10 | €1.10 €3.97 | link (https://www.ebay.de/itm/636ZZ-Kugellager-Rillenlager-Industriequalitat-6x22x7mm-22x6x7mm/222526230665) link | X-bearing Handle Handle | check that fits the window
Hinge | DIN 7954 C 60x60mm | 2 | €1.50 | €3.00 | €4.95 | link (https://www.ebay.de/itm/VORMANN-Scharnier-DIN-7954-C-kantig-verzinkt-M%C3%B6belscharniere-T%C3%BCrscharnier/193033697802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) | Hinge | Enlarge holes to M6
Laser Manual name | Specifications | Amount | Price | Total | Shipping | Vendor1 | Label Name | Notes
Laser Tube Holder | Laser Tube Holders 50-130mm | 2 | €10.00 | €20.00 | €0.00 | link (https://www.ebay.de/itm/2CO2-Laser-Tube-Rohr-Halter-Holder-Halterung-Graviermaschine-Graveurausstattung/392423143545) | Laser Tube Holder | Check screws and plastics are present | about price, best order from China
Laser Tube | 40W CO2 50x720mm | 1 | €85.00 | €85.00 | €0.00 | link (https://www.ebay.de/itm/CO2-Glas-Laserrohr-40W-f%C3%BCr-Laser-Graviermaschine-700mm-Laser-Tube-10-13mA/202857508583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) | Laser Tube | Check the tube is intact | about price, best order from China
Lens | Laser Lens 18mm, 50,8 focal length Mo/Si Mirror 20mm | 1 2 | €30.00 | €30.00 | €0.00 | link (https://www.amazon.de/gp/product/B01ER2IST6/ref=ppx_yo_dt_b_search_asin_title?ie=UTF8&psc=1) | Lens | | about price, best order from China Mirror 20
€2.50 | €4.50

€30.00

link (https://www.aliexpress.com/item/32956947826.html?spm=2114.12010612.8148356.3.7d1b3c8dN3Qiz7) | Mirror 20 | about price, best order from China Mirror 25 | Mo/Si Mirror 25mm | 1 | Mirror 25 | about price, best order from China Mirror Holder 25 | For 25mm mirror | 1 | €14.00 | €14.00 | link | Mirror Holder 25 | Cut base and make new holes; glue base | about price, best order from China Mirror Holder 20 | For 20mm mirror | 1
€25.00 | €25.00 | link (https://www.aliexpress.com/item/33052187457.html?spm=a2g0s.9042311.0.0.44484c4dRmo8LU) | Mirror Holder 20 | Prolongue vertical screw slider; cut the top | about price, best order from China, needs to be cnc milled
Laser Head | For 18mm lens | 1 | Laser Head | Drill laser exit 4.5 | about price, best order from China Rubber Ring | 18mm outer diamter, 1/1.5mm thickness | 4 | Rubber Ring
Fasteners Manual name | Specifications | Amount | Price | Total | Shipping | Vendor1 | Label Name | Notes
B-screw M6-10 | ISO 7380-2 M6 10mm Black | 16 | €0.21 | €3.36 | €0.00 | link (https://eshop.wuerth.de/Product-categories/ISO-7380-2-steel-010.9-plain/14013511180301.cyid/1401.cgid/en/US/EUR/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) | B-screw M6-10 | check if possible from marth0331 ebay instead of würth
B-screw M6-12 | ISO 7380-2 M6 12mm Black | 132 | €0.05 | €6.47 | €6.80 | link (https://www.ebay.de/itm/500-Innensechskant-Linsenflanschschrauben-ISO-7380-2-10-9-schwarz-M6x12/174114047329) | B-screw M6-12
B-screw M6-16 | ISO 7380-2 M6 16mm Black | 71 | €0.05 | €3.48 | | link (https://www.ebay.de/itm/500-Innensechskant-Linsenflanschschrauben-ISO-7380-2-10-9-schwarz-M6x16/174114047398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) | B-screw M6-16
B-screw M6-20 | ISO 7380-2 M6 20mm Black | 22 | €0.05 | €1.08 | | link (https://www.ebay.de/itm/500-Innensechskant-Linsenflanschschrauben-ISO-7380-2-10-9-schwarz-M6x20/174114047513) | B-screw M6-20
T-nut M4 | T-Nut 6 M4 Ball | 4 | €0.27 | €1.08 | | | T-nut M4
T-nut M6 | T-Nut 6 M6 Ball | 175 | €0.27 | €47.08 | €3.90 | link (https://www.ebay.de/itm/251851672402) | T-nut M6
T-nut M3 | Hammer Nut 6 M3 Rotation T-Nut 6 M3 Ball | 25 16 | €0.27 €0.08 | €6.73 €1.20 | T-nut M3 Hammer Nut M3
| Hammer Nut 6 M5 Rotation Hammer Nut 6 M4 Rotation | 12 4 | €0.08 €0.08 | €0.30 €0.90 | | | Hammer Nut M3 Hammer Nut M5 Hammer Nut M5 Hammer Nut M4 Hammer Nut M4
€2.00 | link (https://www.ebay.de/itm/50x-100x-Hammermutter-Nutensteine-M3-M4-M5-M6-T-Nut-fur-EU20-30-40-Aluprofile/402595087410)
Flat Nut M6 | Flatnut M6 | 22 | €0.25 | €5.50 | €6.90 | link (https://www.ebay.de/itm/281925302876) | Flat Nut M6 Washer M6 | DIN 125 M6 | 50 | €0.01 | €0.60
| | | | link (https://www.ebay.de/itm/Unterlegscheiben-Beilagscheiben-Din-125-verzinkt/160641438098) link
DIN 9021 M8 DIN 125 M5 | 8 2 | €0.01 €0.02 | €0.10 €0.04 | | Washer M8 Big Washer M6 Washer M5 Washer M5 Washer M8 Big

Lock Nut M6 | DIN 985 M6 | 48 | €0.01 | €0.48

€5.00

link (https://www.ebay.de/itm/Sicherungsmuttern-Stopmuttern-Muttern-Din-985-verzinkt/150653102538)

Lock Nut M6

Lock Nut M5 | DIN 985 M5 | 8 | €0.01 | €0.08 | Lock Nut M5
Lock Nut M4 | DIN 985 M4 | 8 | €0.01 | €0.08 | Lock Nut M4
Lock Nut M3 | DIN 985 M3 | 16 | €0.01 | €0.16 | Lock Nut M3 Nut M6 | DIN 934 M6 | 10 | €0.01 | €0.10 | Nut M6
B-screw M3-8 | ISO 7380-2 M3 8mm DIN 912 M3 8mm | 20 5 | €0.02 | €0.30 | B-screw M3-8 C-screw M3-8
link (https://www.ebay.de/itm/M3-MaLiMo-DIN-912-Zylinderschrauben-galv-verzinkt-8-8/381944072630) | C-screw M3-8 | recheck price once back in stock
C-screw M3-10 | DIN 912 M3 10mm | 12 | €0.02 | €0.18 | C-screw M3-10 C-screw M3-12 | DIN 912 M3 12mm | 31 | €0.02 | €0.47 | C-screw M3-12 C-screw M3-16 | DIN 912 M3 16mm | 10 | €0.02 | €0.15 | C-screw M3-16 C-screw M3-20 | DIN 912 M3 20mm | 10 | €0.02 | €0.15 | C-screw M3-20 C-screw M3-30 | DIN 912 M3 30mm | 2 | €0.02 | €0.03 | C-screw M3-30 C-screw M4-8 | DIN 912 M4 8mm | 20 | €0.01 | €0.28

link (https://www.ebay.de/itm/M4-MaLiMo-DIN-912-Zylinderschrauben-galv-verzinkt-8-8/311791183620)

| DIN 912 M4 12mm DIN 912 M5 12mm | 10 4 | €0.01 €0.02 | €0.14 €0.06 | C-screw M4-12 C-screw M5-12 C-screw M4-8 C-screw M4-12
link (https://www.ebay.de/itm/M5-MaLiMo-DIN-912-Zylinderschrauben-galv-verzinkt-8-8/381944072599) | C-screw M5-12 C-screw M5-20 | DIN 912 M5 20mm | 8 | €0.02 | €0.12 | C-screw M5-20 C-screw M6-10 | DIN 912 M6 10mm | 3 | €0.02 | €0.07

link (https://www.ebay.de/itm/M6-MaLiMo-DIN-912-Zylinderschrauben-galv-verzinkt-8-8/310573297696)

Standoff | Plastic Screw M3 8mm DIN7985 or similar Plastic Spacer M3 15mm | 16 30 | €0.25 €0.13 | €4.00 €3.90 | €1.95 €0.00 | link (https://www.ebay.de/itm/Abstandhalter-Distanz-Schrauben-Bolzen-H%C3%BClsen-Screw-M3-Kunststoff-PCB-Platinen/174132316372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) link | Plastic-screw M3-8 Standoff | best from China, much cheaper there Plastic-screw M3-8
Bed Leg | Threaded Rod M6 120mm | 4 | €0.60 | €2.40 | €0.00 | link (https://www.ebay.de/itm/Gewindebolzen-M5-M6-M8-M10-Gewindestangen-20-200mm-Stahl-Gewinde-Bolzen-DIN976/124092120957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) | Bed Leg
C-screw M6-10 C-screw M6-20 | DIN 912 M6 20mm | 2 | €0.03 | €0.07 | C-screw M6-20 Hexagon screw M6-30 | DIN 912 M6 30mm | 1 | €0.03 | €0.03 | Hexagon screw M6-30 C-screw M6-35 | DIN 912 M6 35mm | 1 | €0.04 | €0.04 | C-screw M6-35 C-screw M6-40 | DIN 912 M6 40mm | 2 | €0.05 | €0.10 | C-screw M6-40 | recheck price once back in stock Hexagon screw M6-60 | DIN 912 M6 60mm | 1 | €0.07 | €0.07 | Hexagon screw M6-60
Manually produced parts Manual name | Specifications | Amount | Price | Total | Shipping | Vendor1 | Label Name | Notes
Lamella | Bed Lamella, 20x30mm, 400mm length | 30 | €2.18 | €65.40 | €6.95 | link (https://www.ebay.de/itm/Aluminium-Winkel-0-5m-bis-2-0m-Aluprofile-Eckschutz-Winkelblech-Eckprofil-Alu/252502357506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) | Lamella | Smooth them
Mains Cable | AC 3x1.5/2mm 40 cm | 3 | €0.51 | €1.53 | €6.90 | | | Join them together Motor Power Cable
| AC 2x1/1.5mm 110cm | | | | | link (https://www.ebay.de/itm/H05VV-F-PVC-Leitung-Schlauchleitung-flexibles-Kabel-Stromkabel-Ring-100-50-m/272849822469) Emergency Button Cable * | Emergency Button Cable *
Laser Power Cable | AC 3x1.5/2mm 30cm | | | | Laser + Motor Power Cable
| AC 3x1.5/2mm 45cm
LED Cable * | DC 2x1mm 150cm x 2 | 5 | €0.90 | €4.50
DC 4x0.5mm 150cm DC 2x1mm 35cm DC 2x1mm 35cm DC 2x1mm 65cm | link (https://www.ebay.de/itm/272840350273?hash=item3f868d5a41:g:kqwAAOSw~iRZmsbM) X-driver Power Cable Controller Power Cable X-motor Cable * X-driver Power Cable Y-driver Power Cable Y-driver Power Cable Controller Power Cable
| 3 | €1.06 | €3.18 | link (https://www.ebay.de/itm/Steuerleitung-geschirmt-Datenleitung-LIYCY-2-12x0-14-1-5-mm-Schnittlange-lauf-M/283736151360) | check visually Y-driver Logic Cable check visually Switch Cable * | Motor Cables Must be labeled with A- A+ B- B+ Y-motor Cable * X-driver Logic Cable
DC 2x0.25mm 120cm DC 4x0.5mm 45cm DC 4x0.5mm 45cm | X-driver Logic Cable Y-driver Logic Cable
8 | €1.00 | €8.00 Endstop Cable *

DC 2x0.25mm 140cm

DC 2x0.25mm 280cm Water Flow Sensor Cable * | DC 2x0.25mm 50cm
Laser Logic Cable | DC 2x0.25mm 100cm | | | | | | Laser Logic Cable + Resistor | Attach resistor
Laser (-) Cable * | 1x1.5mm 75cm black | 2 | €0.49 | €0.98 | | link (https://www.ebay.de/itm/Fahrzeugleitung-Auto-Kabel-Litze-1-5-bis-6-0-mm-FL-R-YY-FLRY-B-kfz-Kabel/272844404371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) | Laser (-) Cable *
Laser (+) Cable Relay Jumper Cable | jumper cable M-M 20 or 10cm orange! | | | | | | Relay Jumper Cable
Laser Jumper Cable | 1x1/1.5mm 25cm 10cm | | | | | link | Laser Jumper Cable Earth Cable
Jumper Cable | 40 jumper cable M-F 30cm, 5 M-M 30cm DC 2x0.25mm 160cm | 40 1 | €0.08 | €3.08 | €1.99 | link (https://www.ebay.de/itm/40x-Jumper-Kabel-30-cm-M%C3%A4nnlich-Weiblich-Steckbr%C3%BCcke-male-female-dr%C3%A4hte/183673167449) | Jumper Cable Window Sensor Cable *
3D Printed parts Manual name | Specifications | Amount | Price | Total | Shipping | Vendor1 | Label Name | Notes
Exhaust | White/Black PETG+PLA Predator 3D cura profile | 1 1 Radial Fan Connector | €14.00 | €42.00 | €0.00 | Link (https://www.ebay.de/itm/Maertz-Budget-PETG-Filament-Schwarz-Weis-Blau-Rot-Grun-Gelb-1-75mm-2-85mm-1kg/284051614204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) | Exhaust | check parts are smooth; check parts are smooth; Window Magnet Holder check parts are smooth; Window Sensor Holder check parts are smooth; Window Holder check parts are smooth; Wire Fixer
Bed Adjuster | | 4 | | | | | Bed Adjuster | glue nut M6 inside
Piston Support Right | | 1 | | | | | Piston Support Right | check parts are smooth;
Piston Support Left | | 1 | | | | | Piston Support Left | check parts are smooth;
Front Bracket | | 2 | | | | | Front Bracket | check parts are smooth;
Switch Holder | | 1 1 | | | | | Window Magnet Holder Switch Holder | check parts are smooth;
Y-motor Holder | | 1 1 | | | | | Window Sensor Holder Y-motor Holder | check parts are smooth;
X-Endstop Holder | | 1 | | | | | X-Endstop Holder | check parts are smooth;
Front Spacer Right | | 1 | | | | | Front Spacer Right | check parts are smooth;
Front Spacer Left | 25 1 1 | Front Spacer Left Window Holder Wire Fixer | check parts are smooth;
Air Filter Connector * | 2
Emercency Button Cover | 1 | Cover | check parts are smooth
POM 6mm 400x50mm Specifications | Amount | Price | Total | Shipping | Vendor1 | Laser Cut parts Manual name Label Name | Notes Chain Support
| | 1 | €5.00 | €5.00 | €4.90 | link (https://www.ebay.de/itm/POM-schwarz-500x500x6mm-Platte-Zuschnitt-Kunststoff-Halbzeug/112472614381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) | Chain Support | | about price
X-belt Attacher | | 1 | | | | | X-belt Attacher
Y-endstop Holder | | 1 | | | | | Y-endstop Holder
Piston Attacher | POM 10mm | 4 | | | | | Piston Attacher
X-wire Fixer | Acrylic 3mm | 1 | €2.00 | €2.00 | €6.00 | link (https://www.ebay.de/itm/43-99-m-PLEXIGLAS-XT-klar-3-mm-Starke-Kostenfreier-Wunschzuschnitt/193395081159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) | X-wire Fixer | add extra add extra Window
| | 1 | | | | | X-wire Inserter | | about price X-wire Inserter
| Acrylic 6mm 600x800mm | 1 | €36.00 | €36.00 | | link (https://www.ebay.de/itm/PLEXIGLAS-XT-Klar-Materialstarke-Grose-wahlbar-Kostenfreier-Wunschzuschnitt/193564310711) | Window | indicate top and bottom
Focus Tool | | 3 | | | | | Focus Tool
Template 1 | Poplar Wood 5-6mm | 2 | €1.00 | €2.00 | €0.00 | - | Template 1 | | about price, buy from local stores like OBI Template 2
| Poplar Wood 5-6mm | 2 | €1.00 | €2.00 | | | Template 2
CNC Parts Manual name | Specifications | Amount | Price | Total | Shipping | Vendor1 | Label Name | Notes Converter PCB | FR1/2 with Logic converter Attiny45/85 | 1 | €10.00 | €10.00 | €0.00 | - | Converter PCB | program and test it | selfmade, may be possible to produce it
Laser Head Holder | CNC grade Aluminum 50x50x100mm | 1 | €34.00 | €34.00 | €0.00 | link (https://www.ebay.de/itm/Aluminium-Vierkant-Vierkantstange-Stab-AlCuMgPb-Alu-Block-Vierkantmaterial/122358237569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) | Laser Head Holder | smooth | from Schneiders CNC
Front Pulley Holder | CNC grade Aluminum flat 6mm AlMg3 | 2 | €21.00 | €21.00 | €5.90 | link (https://www.ebay.de/itm/Aluminiumplatte-AlMg3-Abmessungen-wahlbar-Aluplatte-Alu-Blende-Blech-Platte-Walz/383467300487) | Front Pulley Holder | smooth; tapping and position marking Insert Y-Bearing Back; rub edges Chain End Holder | single place 500/400x200mm is sufficient
Back Bearing Holder | CNC grade Aluminum flat 6mm AlMg3 CNC grade Aluminum flat 6mm AlMg3 | 2 1 | | | | | Back Bearing Holder Chain End Holder | smooth
X-holder Right | CNC grade Aluminum flat 6mm AlMg3 | 1 | | | | | X-holder Right | smooth
X-holder Left | CNC grade Aluminum flat 6mm AlMg3 | 1 | | | | | X-holder Left | smooth
Back Panel | Dibond 3mm Black matte, 2 plates 1000x1500mm | 1 | €70.00 | €70.00 | €44.00 | link (https://onlineshop.firstbond.de/Aluminium-Verbundplatten/AluVerbundplatten--3mm-Farbig-matt/AluVerbundplatte-3mm-3050x1500mm-Anthrazit-RAL7016---S.html) | Back Panel | attach or engrave labels; smooth smooth Right Panel | about prices, 2/3 of a plate are used
Front Panel | | | | | | | Front Panel | attach writings
Top Back Panel | | | | | | | Top Back Panel | smooth
Top Front Panel | | | | | | | Top Front Panel | smooth
Laser Panel | | | | | | | Laser Panel | smooth
Sub Panel Right | | | | | | | Sub Panel Right | smooth
Sub Panel Left | | | | | | | Sub Panel Left | smooth
Sub Panel Front | | | | | | | Sub Panel Front | smooth
Spacer Panel Right | | | | | | | Spacer Panel Right | smooth
Spacer Panel Left | | | | | | | Spacer Panel Left Right Panel | smooth
Left Panel | | | | | | | Left Panel | smooth
Air Panel | | | | | | | Air Panel | smooth Air Panel
Bottom Panel | Dibond 3mm Gray matte RAL 9006 | 1 | €30.00 | €30.00 | | link (https://onlineshop.firstbond.de/Aluminium-Verbundplatten/AluVerbundplatten--3mm-Farbig-matt/3mm-Silber-1000x2100mm--RAL9006-126.html) | Separator Panel Bottom Panel | | about prices, 2/3 of a plate are used Separator Panel

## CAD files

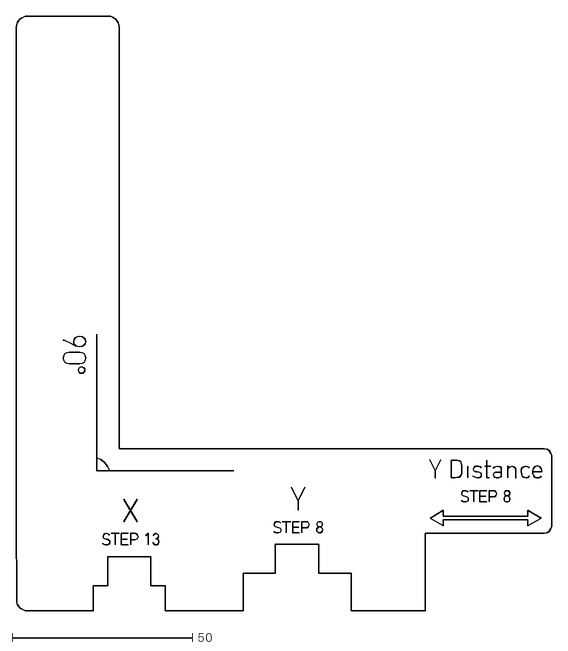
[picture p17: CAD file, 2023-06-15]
Fabulaser_Mini_V2/cad/Template 1.dxf
148.5 x 165.0

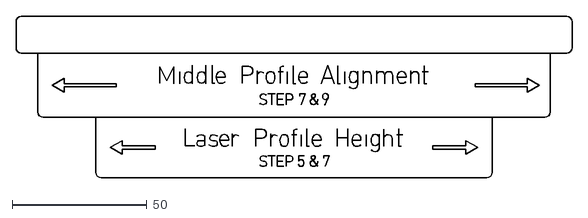
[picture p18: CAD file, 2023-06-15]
Fabulaser_Mini_V2/cad/Template 2.dxf
206.2 x 59.9

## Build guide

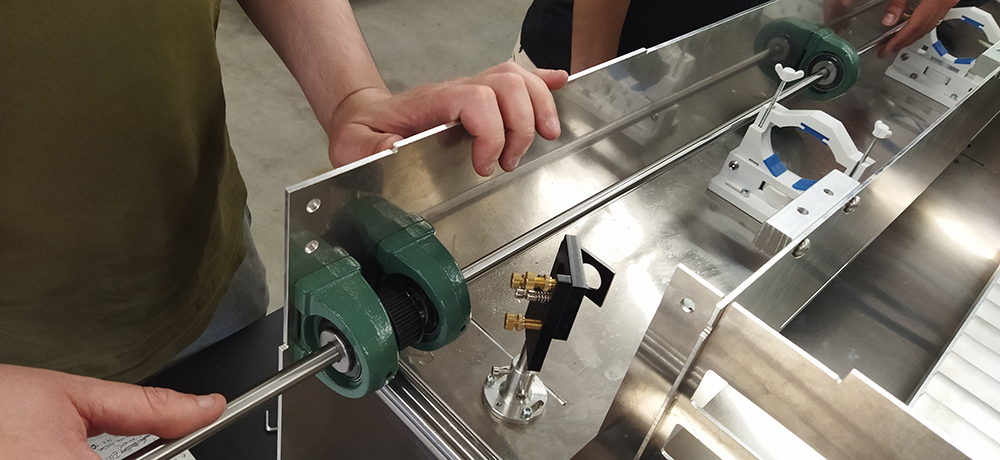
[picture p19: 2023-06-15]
media/MachineBuilding1.jpg

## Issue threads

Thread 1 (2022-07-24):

mechanical backlash in Y-axis

hanebefl, 2022-07-24:
## issue
The Fabulaser machines I've seen all have a small issue with what I (until now) assumed is backlash in the Y-axis. This is well visible with marking or cutting small circles: There are small "edges" at the top right and bottom left (when cutting clockwise).
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

I've managed to pinpoint the location of the backlash to the couplers, connecting the Y-motor to the Y-shafts.

## setup
To verify this location, I've attached two levers to a coupler (one at the motor side, one at the shaft side) and placed a dial indicator on them.
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

Next I've created a gcode file which moves the Y-axis back and forth ten times, first one step, then two steps, then three and so on. To not lose count of the number of steps, the X-axis moves for 5mm between each cycle. The gcode file and python script generating the gcode, are attached here:
[backlash-gcode-and-py.zip](https://github.com/fab-machines/Fabulaser-Mini/files/9176003/backlash-gcode-and-py.zip)

I've defined the backlash as first measurement that actually moves the needle of the dial indicator back and forth. Some movement in only one direction can be observed first, but this is just part of the backlash itself.

## findings
With this setup, the dial indicator shows a back-and-forth movement at the motor side at 4 steps (or 0.045 mm) travel. At the shaft side the back-and-forth movement is only detected at 15 or 16 steps (0.169 mm). This confirms a backlash of 0.124 millimeters in the couplers.

Here you can see two animations, with the number of steps moved (sorry for the shaky camera):
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
In the second animation you can actually see movement of the left "motor" lever, while the right "shaft" lever is standing still.

## next steps
There seems to be a lot of resistance in the movement of the Y-axis. One area I've detected is the 'Y-pulley front'. I've got an idea for a different design, and will report my findings.

Maybe there's a different type of coupler, that less backlash at the same torque?

satshas, 2022-07-24:
First of all **many thanks** for the time you took to test this out and also to verify it with the dial indicators.

Seems definitively as you argue, with the couplers flexing a bit while the Y axis is moving (assuming the guides+bearings are lubricated and the rest of the assembly is well done). The Y-Pulley front design is also worth a change to improve smoothness as it is hold only on one side.

We're currently making the large format Laser and we took many of these parameters into account, even decoupling the Y motor from the Y shaft/belts. We'll probably share them in the next release of Fabulaser, if they prove to be good on the large design. In the meantime if your findings are good we can add them to the repository.

In the design of the CNC Milling machine we started using these couplers, maybe worth to try them also on Fabulaser?

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

satshas, 2023-12-22:
Solved in Fabulaser Mini V3

Closed 2023-12-22.

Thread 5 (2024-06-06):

Security labels

jcolomb, 2024-06-06:
there is a need for specific stickers:
- laser class 1 equipment
- label on the window (is it special glass filtering laser light ?)
- operate with safety googles when open

Also we need a manual indicating:
- safety precautions for use (danger of fire, event of a power failure)
    - danger of fire
    - event of a power failure `*`
    - residual risks (Exposure to Laser radiation, Ejected Material, Noise Exposure, Chemical Hazards, Mechanical Hazards)
- safety precautions for maintenance/calibration (when open): googles

Safety tools:
- the kit should be delivered with safety googles. Alternatively a source of which googles to buy should be indicated

`*` This may include:
* Press the emergency stop button or activate the emergency stop control as soon as possible to halt all machine functions.
- Notify relevant personnel, including supervisors, maintenance staff, and safety officers, of the power failure.
- Provide clear and concise information about the situation, including the cause of the power failure and any immediate actions taken.
- Power down the machine in a safe and controlled manner, taking care to secure moving parts and ensure proper ventilation.
- If the power failure poses a significant safety risk or if evacuation procedures dictate, evacuate personnel from the area surrounding the machine.

jcolomb, 2024-06-06:
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

satshas, 2024-06-11:
Thanks for the feedback, I will pass it to the people taking care of stickers and manual.

MAI99SONI, 2024-07-02:
Could you please provide an update on this issue?

satshas, 2025-01-06:
Sorry for the late reply. The information will be updated on the new version of the machine.

Closed 2025-01-06.

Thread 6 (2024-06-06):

Settings for cutting papers

jcolomb, 2024-06-06:
Did you ever try to cut papers (we plan to create book marks as goodies).

Any tips on the settings we should try ?

satshas, 2024-06-07:
Hello there,

We have been successful in cutting materials like "Finnpappe" "Finncardboard", thick paper (>=0.5mm) and normal cardboard.

As a starting point you could try the following:

- power between 10 and 20%
- speed between 3 and 10%

Closed 2024-06-17.

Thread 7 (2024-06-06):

Stop button info

jcolomb, 2024-06-06:
Does the emergency stop button follow the  EN ISO 13850 and EN/IEC 60204-
1 standards ?

satshas, 2024-06-11:
Hello,

Yes, we checked both norms an it is according to both standards.

If you need specific details please contact me directly so I can put you in touch with the person taking care of it, or if you would like to give feedback or any mistake is present.

daniele@inmachines.net

Closed 2024-06-17.

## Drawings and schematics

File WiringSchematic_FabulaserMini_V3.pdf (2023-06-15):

# OLSK SMALL LASER V1.5

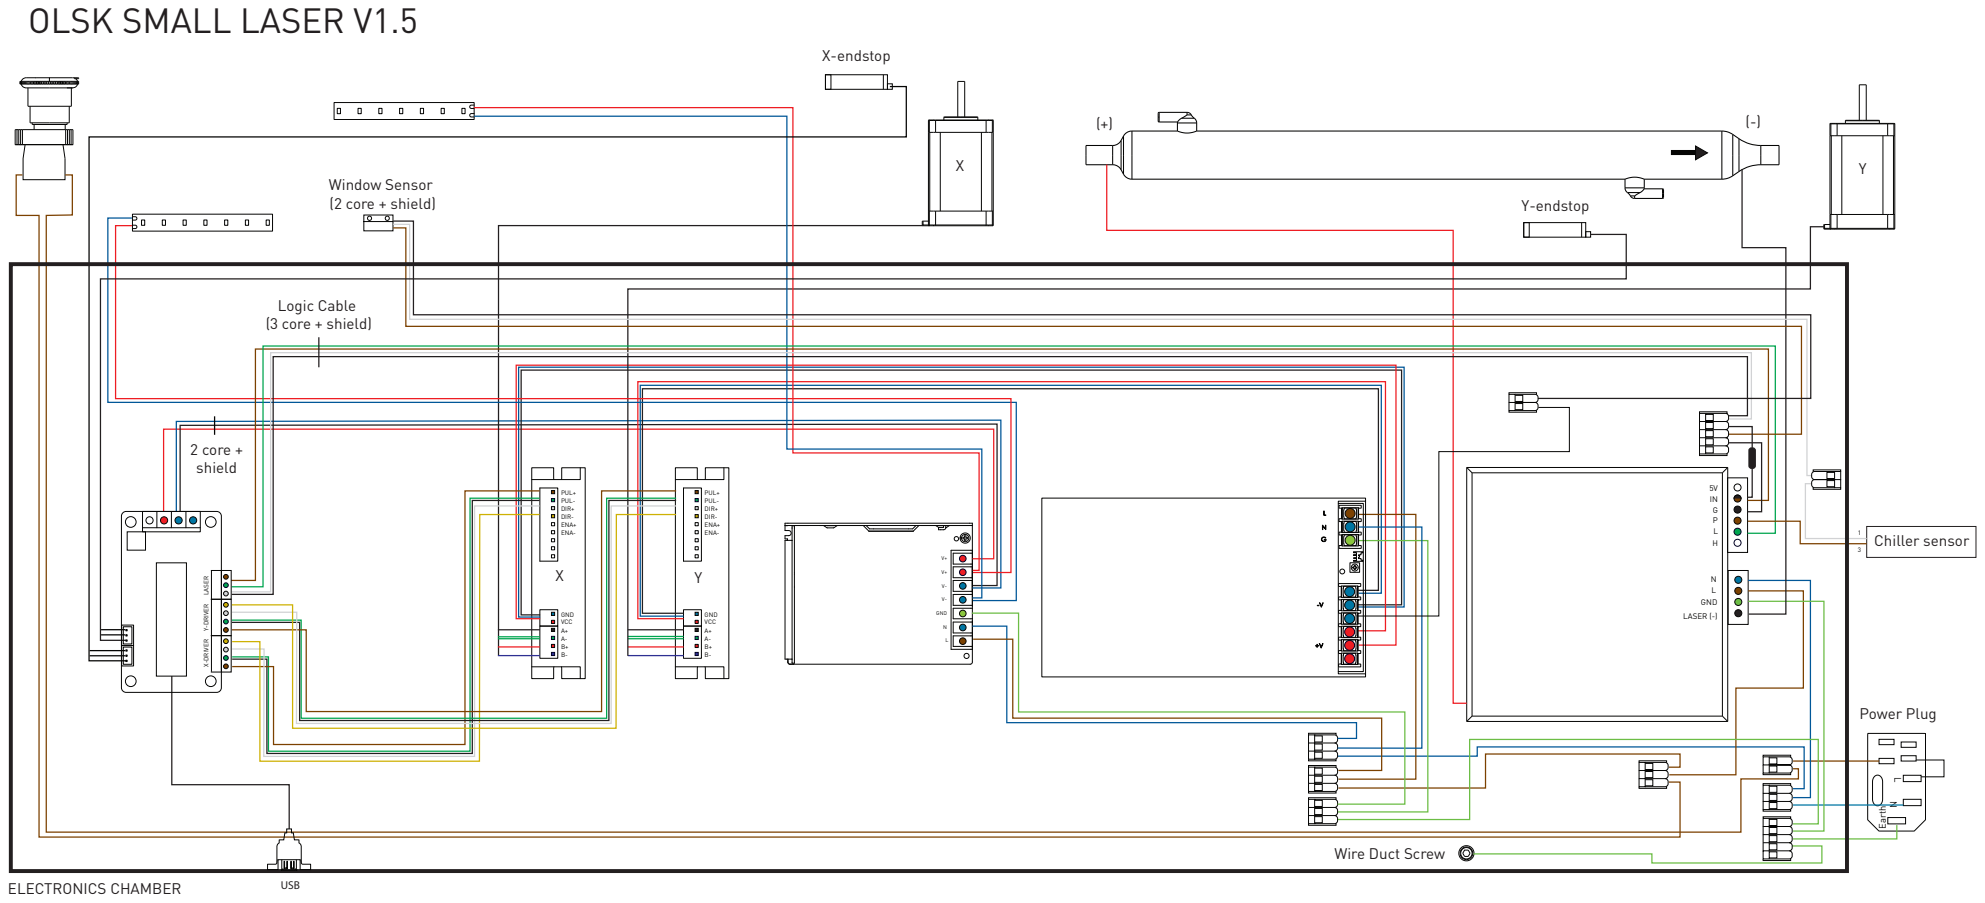
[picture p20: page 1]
GND LASER (-); GND VCC; ENA-; PUL+ PUL-; ENA+; DIR+ DIR-; Earth L; GND; Chiller sensor; Y-endstop; X-endstop; Window Sensor (2 core + shield); Power Plug; Logic Cable (3 core + shield); USB; ELECTRONICS CHAMBER; 2 core + shield

LASER Y-DRIVER X-DRIVER

Wire Duct Screw

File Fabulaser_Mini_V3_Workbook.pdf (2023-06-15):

Step
Number | Step Title | | Parts list | | Tools list
Remarks
| | Quantity | Part name | Quantity | Tool name
01 | Bottom Panel | 1 | Bottom Panel | 1 | Allen Key 5.0

Do not tighten the screws yet for further alignment.

| | 6 | B-screw M8-10
| | | | 1 | Allen Key 4.0

On the right profile, insert T-nuts M5 and attach it to the Bottom Panel, with the cable duct on top.

| | 3 | B-screw M5-12 | 1 | Ruler

Position the cable duct starting about 45 mm from the front of the machine.

| | 3 | Profile 30-800
| | 1 | Cable Duct
| | 8 | T-nut M8
| | 4 | T-nut M5
02 | Attach Electronics | 2 | Motor Driver | 1 | Allen Key 2.5
All motor drivers should have the terminals pointing outwards.
| | 1 | Laser Power Supply
| | 1 | Controller PCB
| | 4 | Plastic Screw M3-8
| | 4 | Standoff M3 MF
| | 8 | B-screw M4-10

### 03.1 Inner Right Panel

| | 1 | Inner Right Panel | 1 | Allen Key 3.0

Attach the parts before inserting the panel in the Bottom Panel.
1 | Logic Power Supply | The Cable Glands should be turned
to the inside
| | 1 | Motor Power Supply
| | 3 | C-screw M3-6
| | 10 | B-screw M4-10
| | 2 | Cable Glands
| | 6 | Wire Fixers

### 03.2 Y-motor

| | 1 | Cable Duct
| | | | 1 | Allen Key 3.0

Fix the pulley on the motor shaft aligning it to the edge, with the setscrews towards the outer side.

Step Number | Step Title | Parts list | Tools list | Remarks
Quantity | Part name | Quantity | Tool name
5 | C-screw M4-10 | 1 | Wrench 5.5

Tighten the set screws of the pulley to the flat part of the motor shaft.
4 | Lock Nut M5 | Insert the belt before fixing the motor
on Y-motor Holder.
1 | Y-motor Belt

Fix the cable duct after attaching the motor. They should not be touching each other.
1 | Y-motor Pulley | The cables of the motor should be
pointing inside or down
1 | Y-motor
1 | Y-motor Holder
2 | B-screw M8-16
4 | C-screw M5-30

### 04 Inner Left Panel and Middle Panel

1 | Inner Left Panel
| | 1 | Allen Key 5.0

The side hole of the Middle Panel needs to point to the left of the machine (from the front view).
1 | Middle Panel
2 | Hinge Support
4 | B-screw M8-30
4 | Lock Nut M8

### 05 Laser Panel

1 | Laser Panel
| | 1 | Allen Key 3.0

The base of the First Mirror Holder should be fixed upside-down on the bottom of the Laser Panel.

1 | First Mirror Holder | 1 | Allen Key 4.0

Use loctite to fix the rod of the First Mirror Holder

2 | Laser Tube Holder
8 | C-screw M5-16
2 | B-screw M4-10

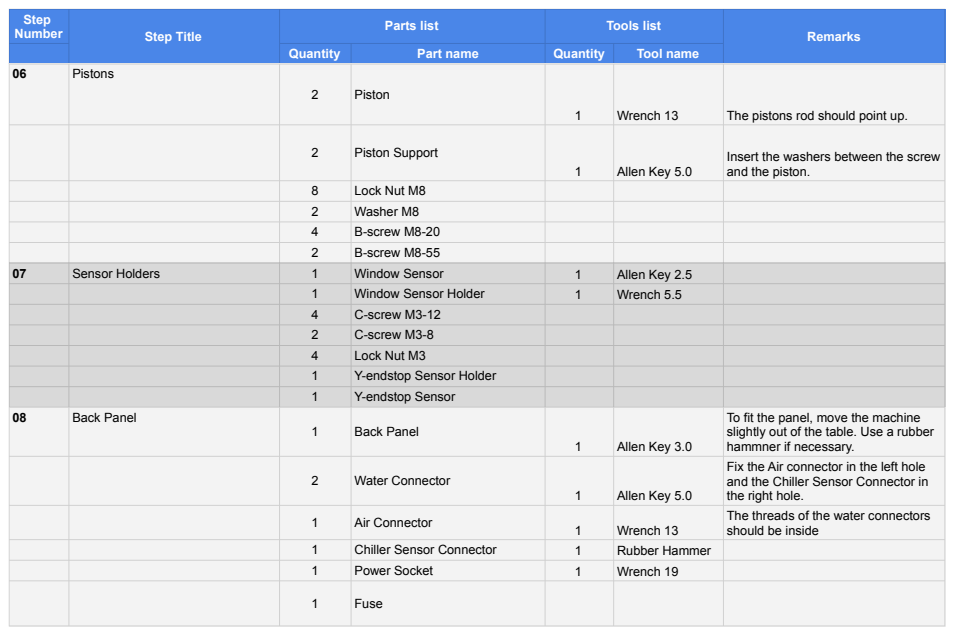
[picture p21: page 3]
06 Pistons; Piston; Wrench 13; The pistons rod should point up.; Piston Support; Allen Key 5.0; Lock Nut M8; Washer M8; B-screw M8-20; B-screw M8-55; Sensor Holders; Window Sensor; Allen Key 2.5; Window Sensor Holder; Wrench 5.5; C-screw M3-12; C-screw M3-8; Lock Nut M3; Y-endstop Sensor Holder; Y-endstop Sensor; 08 Back Panel; Back Panel; Allen Key 3.0; Water Connector; Air Connector; Chiller Sensor Connector; Rubber Hammer; Power Socket; Wrench 19; Fuse

Step Number | Step Title | Parts list | Tools list | Remarks

Quantity | Part name | Quantity | Tool name

Insert the washers between the screw
and the piston.

To fit the panel, move the machine
slightly out of the table. Use a rubber
hammner if necessary.
Fix the Air connector in the left hole
and the Chiller Sensor Connector in
the right hole.
The threads of the water connectors
should be inside

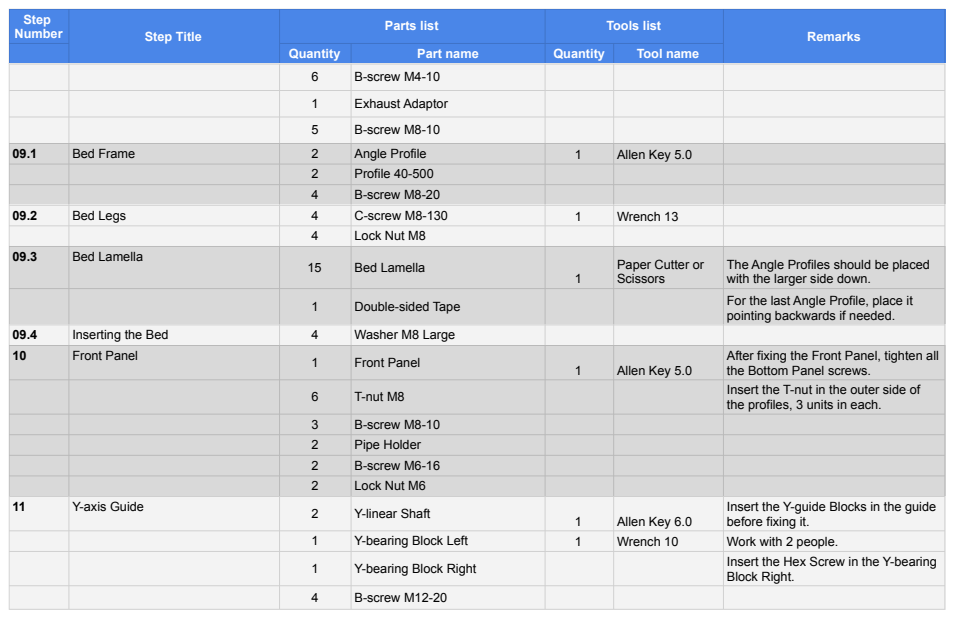
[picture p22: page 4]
B-screw M4-10; Exhaust Adaptor; B-screw M8-10; Bed Frame; Angle Profile; Allen Key 5.0; Profile 40-500; B-screw M8-20; Bed Legs; C-screw M8-130; Wrench 13; Lock Nut M8; 09.3 Bed Lamella; Bed Lamella; Double-sided Tape; For the last Angle Profile, place it; Inserting the Bed; Washer M8 Large; Front Panel; T-nut M8; Insert the T-nut in the outer side of; Pipe Holder; B-screw M6-16; Lock Nut M6; Y-axis Guide; Y-linear Shaft; Allen Key 6.0; Y-bearing Block Left; Wrench 10; Work with 2 people.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

Step Number | Step Title | Parts list | Tools list | Remarks

Quantity | Part name | Quantity | Tool name

Paper Cutter or
Scissors

The Angle Profiles should be placed
with the larger side down.

pointing backwards if needed.

After fixing the Front Panel, tighten all
the Bottom Panel screws.

the profiles, 3 units in each.

Insert the Y-guide Blocks in the guide
before fixing it.
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

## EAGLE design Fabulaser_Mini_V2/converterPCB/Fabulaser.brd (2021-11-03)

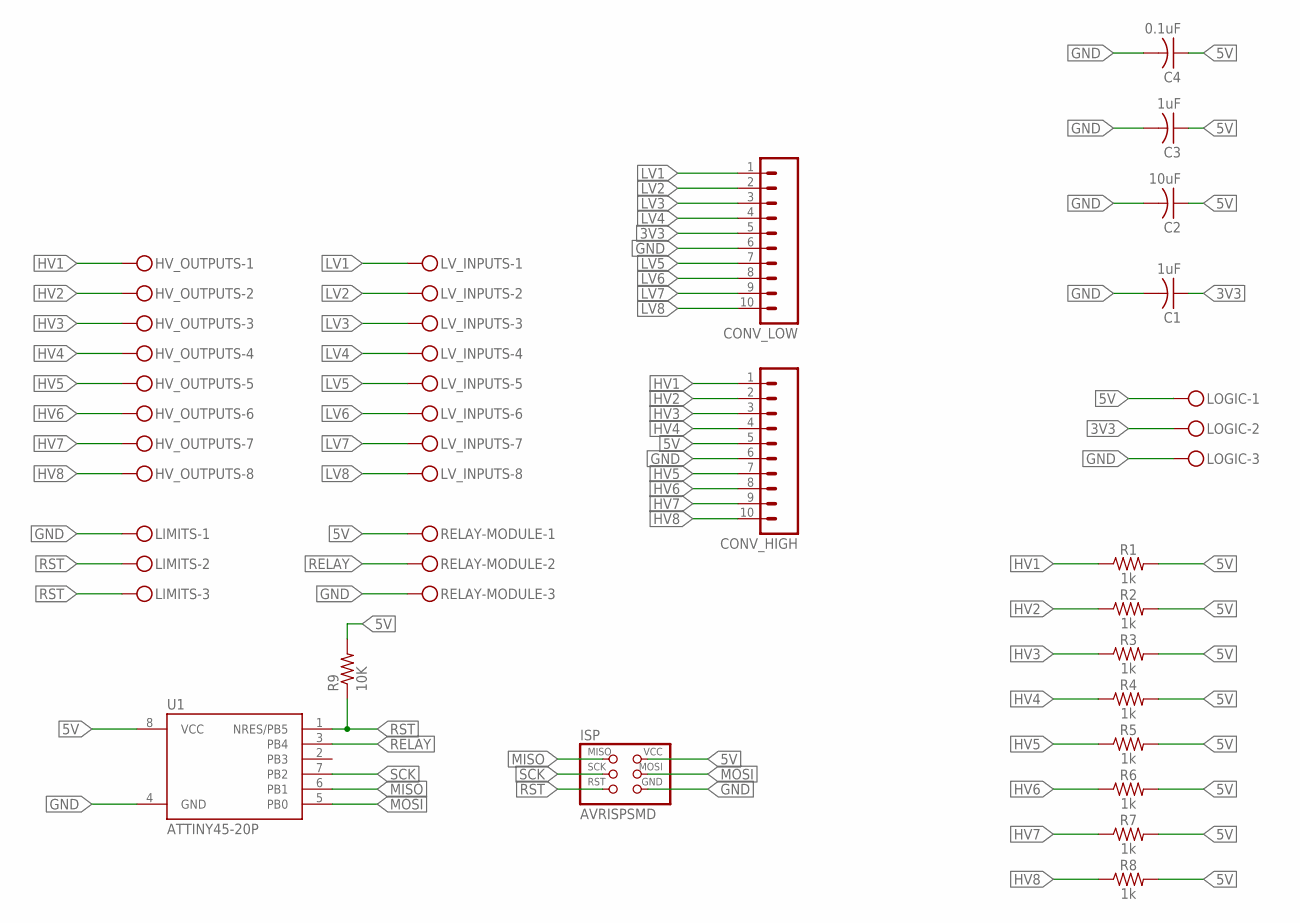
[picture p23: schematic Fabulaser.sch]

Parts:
C1, C3: 1uF; C1206FAB
C2: 10uF; C1206FAB
C4: 0.1uF; C1206FAB
CONV_HIGH: M10; 10P
CONV_LOW: M10; 10P
HV_OUTPUTS: MKDSN1,5/8-5,08
ISP: AVRISPSMD; 2X03SMD
LIMITS: MKDSN1,5/3-5,08
LOGIC: MKDSN1,5/3-5,08
LV_INPUTS: MKDSN1,5/8-5,08
R1, R2, R3, R4, R5, R6, R7, R8: 1k; AXIAL-0.3
R9: 10K; R1206FAB
RELAY-MODULE: MKDSN1,5/3-5,08
U1: ATTINY45-20P; PDIP08_300MIL

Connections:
3V3: C1.1, CONV_LOW.5, LOGIC.2
5V: C2.1, C3.1, C4.1, CONV_HIGH.5, ISP.2 (VCC), LOGIC.1, R1.P$2 (2), R2.P$2 (2), R3.P$2 (2), R4.P$2 (2), R5.P$2 (2), R6.P$2 (2), R7.P$2 (2), R8.P$2 (2), R9.2, RELAY-MODULE.1, U1.8 (VCC)
GND: C1.2, C2.2, C3.2, C4.2, CONV_HIGH.6, CONV_LOW.6, ISP.6 (GND), LIMITS.1, LOGIC.3, RELAY-MODULE.3, U1.4 (GND)
HV1: CONV_HIGH.1, HV_OUTPUTS.1, R1.P$1 (1)
HV2: CONV_HIGH.2, HV_OUTPUTS.2, R2.P$1 (1)
HV3: CONV_HIGH.3, HV_OUTPUTS.3, R3.P$1 (1)
HV4: CONV_HIGH.4, HV_OUTPUTS.4, R4.P$1 (1)
HV5: CONV_HIGH.7, HV_OUTPUTS.5, R5.P$1 (1)
HV6: CONV_HIGH.8, HV_OUTPUTS.6, R6.P$1 (1)
HV7: CONV_HIGH.9, HV_OUTPUTS.7, R7.P$1 (1)
HV8: CONV_HIGH.10, HV_OUTPUTS.8, R8.P$1 (1)
LV1: CONV_LOW.1, LV_INPUTS.1
LV2: CONV_LOW.2, LV_INPUTS.2
LV3: CONV_LOW.3, LV_INPUTS.3
LV4: CONV_LOW.4, LV_INPUTS.4
LV5: CONV_LOW.7, LV_INPUTS.5
LV6: CONV_LOW.8, LV_INPUTS.6
LV7: CONV_LOW.9, LV_INPUTS.7
LV8: CONV_LOW.10, LV_INPUTS.8
MISO: ISP.1 (MISO), U1.6 (PB1)
MOSI: ISP.4 (MOSI), U1.5 (PB0)
RELAY: RELAY-MODULE.2, U1.3 (PB4)
RST: ISP.5 (RST), LIMITS.2, LIMITS.3, R9.1, U1.1 (NRES/PB5)
SCK: ISP.3 (SCK), U1.7 (PB2)

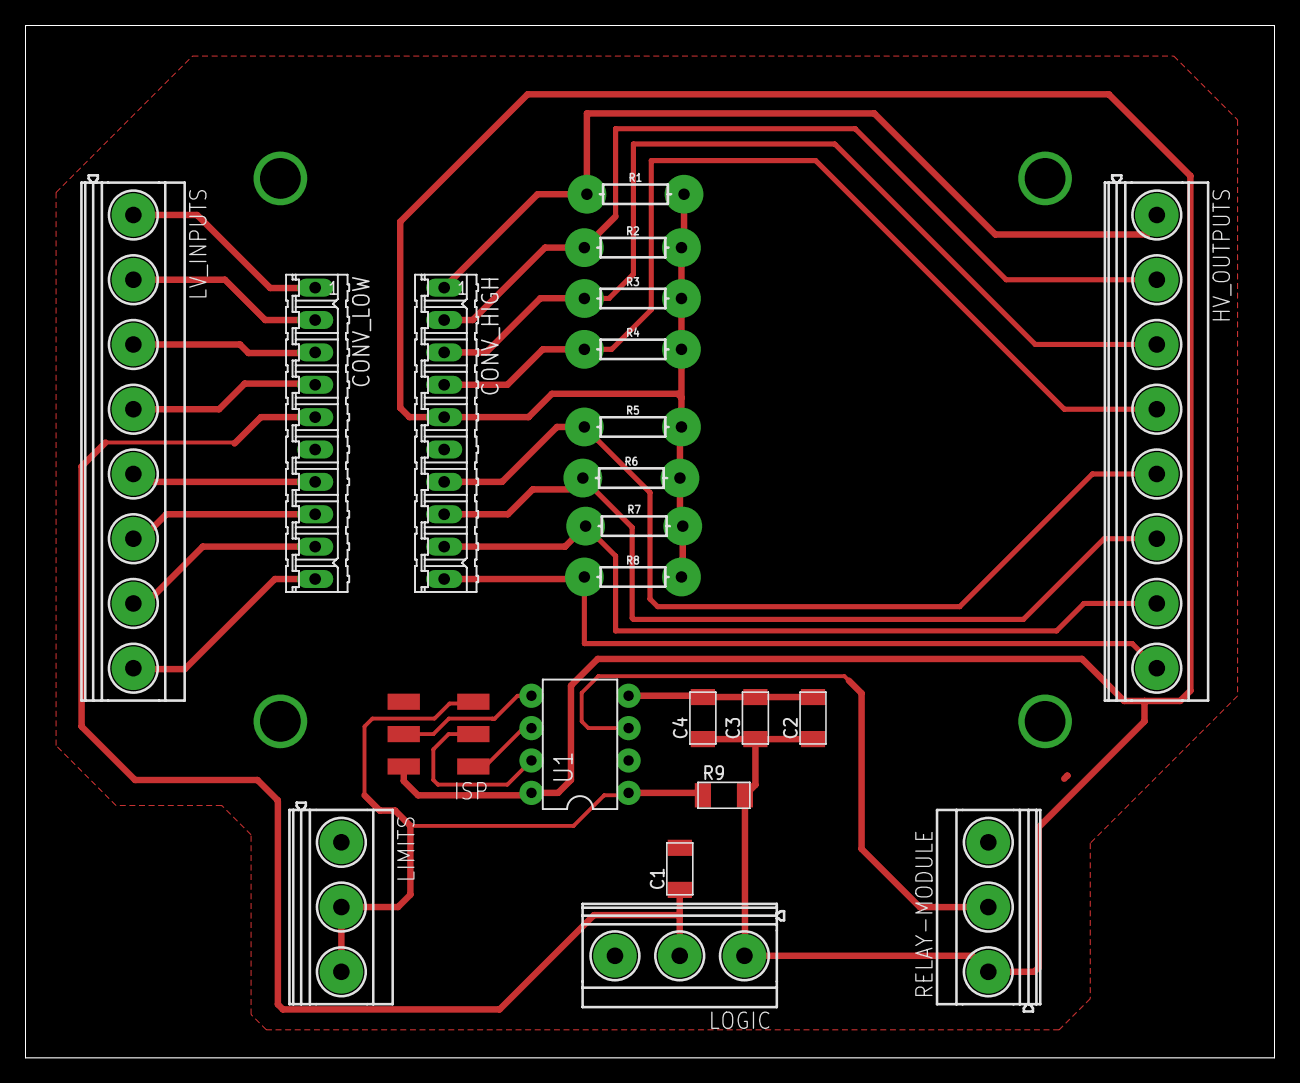
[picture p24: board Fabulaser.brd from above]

Board: 2 copper layers, 98.0 x 81.0 mm, 22 parts (0 on the bottom side), 24 nets.

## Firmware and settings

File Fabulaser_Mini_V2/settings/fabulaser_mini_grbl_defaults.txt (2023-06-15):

$0 = 10    (Step pulse time, microseconds)
$1 = 100    (Step idle delay, milliseconds)
$2 = 0    (Step pulse invert, mask)
$3 = 1    (Step direction invert, mask)
$4 = 0    (Invert step enable pin, boolean)
$5 = 1    (Invert limit pins, boolean)
$6 = 0    (Invert probe pin, boolean)
$10 = 0    (Status report options, mask)
$11 = 0.010    (Junction deviation, millimeters)
$12 = 0.002    (Arc tolerance, millimeters)
$13 = 0    (Report in inches, boolean)
$20 = 0    (Soft limits enable, boolean)
$21 = 0    (Hard limits enable, boolean)
$22 = 0    (Homing cycle enable, boolean)
$23 = 1    (Homing direction invert, mask)
$24 = 50.000    (Homing locate feed rate, mm/min)
$25 = 6000.000    (Homing search seek rate, mm/min)
$26 = 250    (Homing switch debounce delay, milliseconds)
$27 = 2.000    (Homing switch pull-off distance, millimeters)
$30 = 100    (Maximum spindle speed, RPM)
$31 = 0    (Minimum spindle speed, RPM)
$32 = 1    (Laser-mode enable, boolean)
$33 = 5000.000   
$34 = 0.000   
$35 = 1.000   
$36 = 100.000   
$100 = 89.000    (X-axis travel resolution, step/mm)
$101 = 89.000    (Y-axis travel resolution, step/mm)
$102 = 160.000    (Z-axis travel resolution, step/mm)
$103 = 160.000   
$110 = 24000.000    (X-axis maximum rate, mm/min)
$111 = 20000.000    (Y-axis maximum rate, mm/min)
$112 = 24000.000    (Z-axis maximum rate, mm/min)
$113 = 24000.000   
$120 = 1800.000    (X-axis acceleration, mm/sec^2)
$121 = 500.000    (Y-axis acceleration, mm/sec^2)
$122 = 2500.000    (Z-axis acceleration, mm/sec^2)
$123 = 2500.000   
$130 = 300.000    (X-axis maximum travel, millimeters)
$131 = 200.000    (Y-axis maximum travel, millimeters)
$132 = 50.000    (Z-axis maximum travel, millimeters)
$133 = 100.000   
$140 = 0.600   
$141 = 0.600   
$142 = 0.000   
$143 = 0.000   

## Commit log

2021-11-03 added BOM, firmware and updated readme
2021-11-03 added CAD files, converter PCB
    [Fabulaser.brd, Fabulaser.sch]
2021-11-03 updated grbl defaults
    [fabulaser_mini_grbl_defaults.txt]
2022-05-24 Added template DXF files
    [Template 1.dxf, Template 2.dxf]
2023-06-15 Fabulaser Mini v2 folder
    [Fabulaser.brd, Fabulaser.sch, Template 1.dxf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]
2025-08-13 add assembly manual
2025-08-13 update assembly manual
2025-08-27 Assembly Manual json update
2025-08-27 Assembly Manual update package
2025-08-27 Assembly Manual package update
2025-08-27 Assembly Manual update
2026-01-30 added relay code

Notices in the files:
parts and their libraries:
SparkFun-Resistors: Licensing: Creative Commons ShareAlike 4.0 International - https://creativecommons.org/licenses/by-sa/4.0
